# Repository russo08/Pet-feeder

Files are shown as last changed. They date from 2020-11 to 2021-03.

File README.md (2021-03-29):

# Pet-Feeder
Arduino based pet feeder

## Libraries
Here are all the libraries you will need to download  
https://github.com/JChristensen/JC_Button - Buttons library  
https://github.com/VaSe7u/LiquidMenu - Creating the menu  
https://github.com/adafruit/RTClib - Getting time from the RTC  

## 3D Printed Models

All printed using an Ender 3 pro and with the following settings
- Material: PLA+
- Nozzle Temp: 210 C
- Bed Temp: 60 C
- Print speed: 60 mm/s
- Slicer Settings: Use Standard default Cura settings (except printing temp and print speed)

## Funnel, Servo Bracket, and Food Chute, and Chute Rail Supports
- Support Density: 10% for all
- Support placement for funnel: Touching buildplate
- Support placement for bracket: Everywhere
- Support placement for food chute: Touching buildplate
- Support placement for chute rail: Touching buildplate

## Model Orientation in slicer
- Print chute rail standing up with rear (closed off section) touching the build plate
- Print bracket with front touching build plate for minimal support

**NOTE:** The food chute takes up the maximum amount of print surface from the Ender 3. If you plan on using 
a printer with a smaller bed size, the food chute will not fit. In order to get the chute to fit on the slicer, the bottom of the chute 
should be touching the build plate and oriented diagonally on the build surface. It takes a little messing around with, but it will
eventually snap into place.

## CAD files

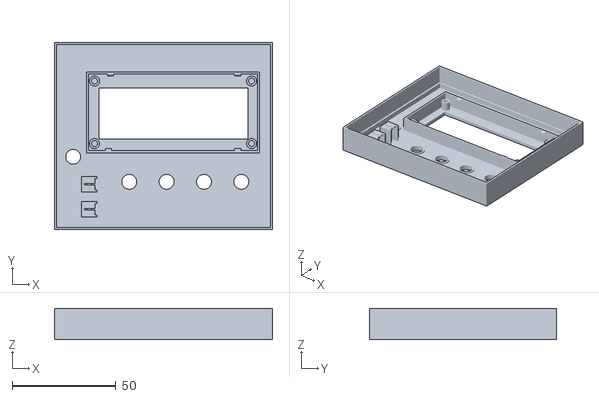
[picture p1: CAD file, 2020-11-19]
STLs/Enclosure_lid2.stl
105.0 x 90.0 x 15.0

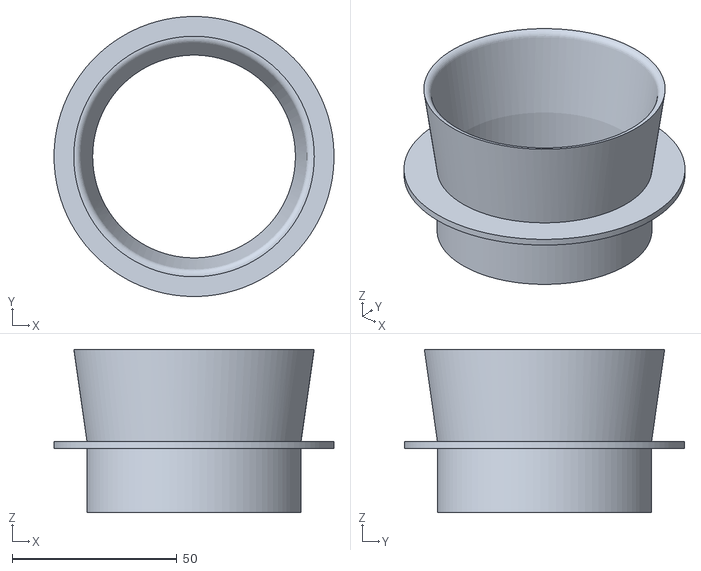
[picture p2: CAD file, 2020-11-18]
STLs/Food_funnel.stl
85.0 x 85.0 x 49.5

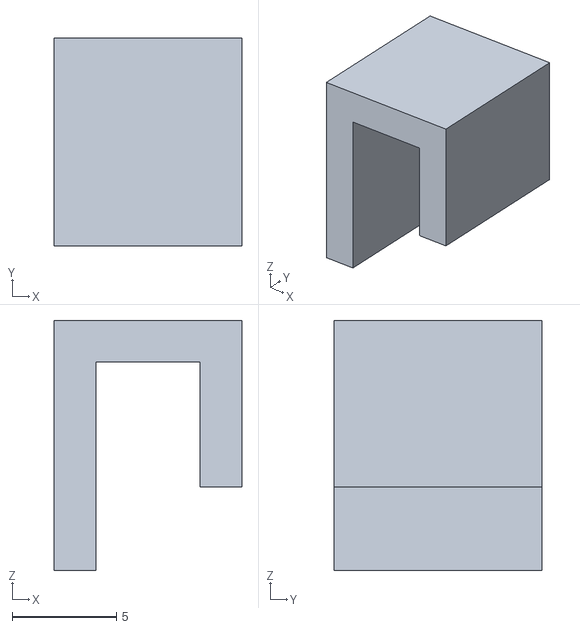
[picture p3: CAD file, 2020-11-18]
STLs/Wire_clip.stl
9.00 x 10.0 x 12.0

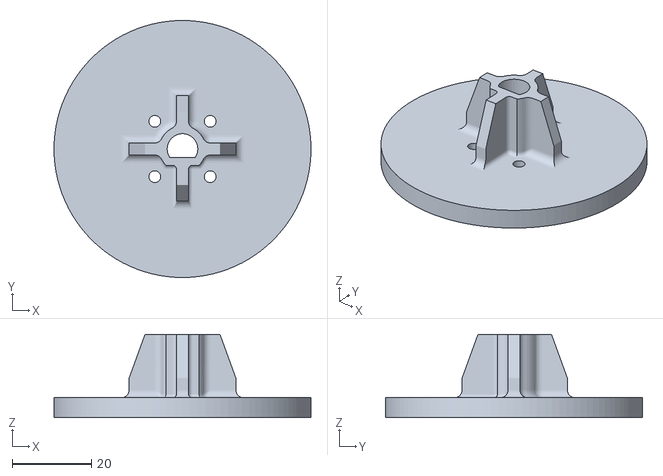
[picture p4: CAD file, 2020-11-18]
STLs/Encoder_Wheel.stl
65.0 x 65.0 x 21.0

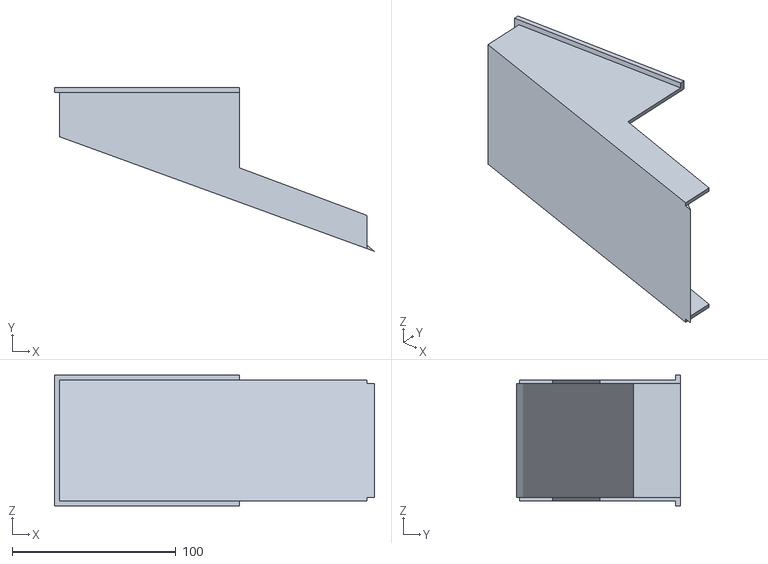
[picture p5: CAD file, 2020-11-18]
STLs/Food_Chute.stl
195.6 x 100.1 x 80.0

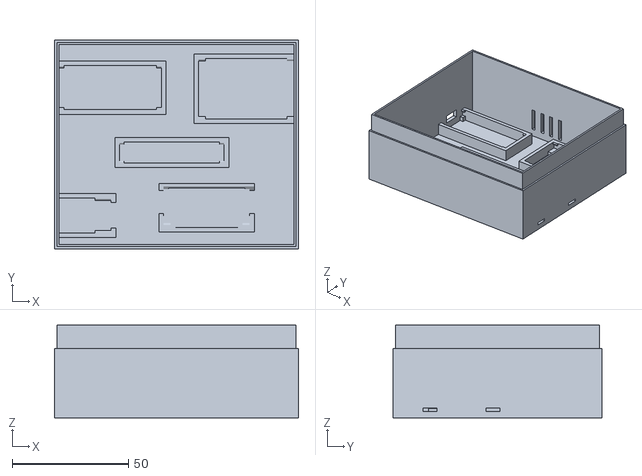
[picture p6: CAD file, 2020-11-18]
STLs/Fedder_Enclosure_bottom.stl
105.0 x 90.0 x 40.0

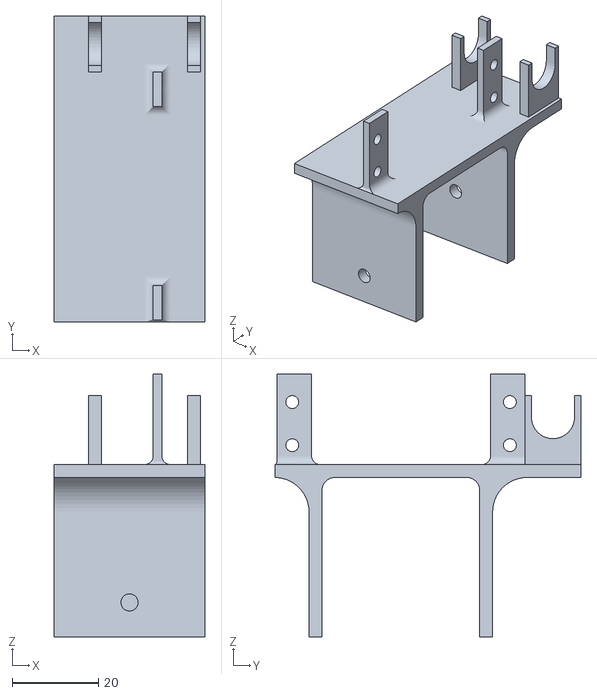
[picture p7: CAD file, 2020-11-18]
STLs/Servo_bracket.stl
35.0 x 71.0 x 61.0

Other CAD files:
Fusion_360_files/Enclosure_lid2 .f3d
Fusion_360_files/Encoder_Wheel.f3d
Fusion_360_files/Fedder_Enclosure_bottom.f3d
Fusion_360_files/Food_Chute v4.f3d
Fusion_360_files/Food_funnel.f3d
Fusion_360_files/Servo_bracket v13.f3d
Fusion_360_files/Wire_clip v2.f3d
Fusion_360_files/Wire_clip.f3d

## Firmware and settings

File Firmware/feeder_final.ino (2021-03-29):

// Final version for the pet feeder

/*  Features:
    - Easy to navigate menu
    - Overview of feed times, current time, feeding comletions,
      and feeding portion on the main screen
    - Controllable portions using a hall sensor for feedback
    - Accurate time keeping with DS1307 chip
    - Can manually change set time in DS1307 chip
    - Two feedings per day
    - Manual feeding option
    - Feeding restart in case of power outtage
    - LED indication of hall sensor and real time clock
    - Feeding times and completions safetly store in EEPROM
    - Servo "jiggle" in the event of food getting stuck
*/

#include <JC_Button.h>
#include <Wire.h>
#include <LiquidCrystal_I2C.h>
#include <LiquidMenu.h>
#include <RTClib.h>
#include <Servo.h>
#include <EEPROM.h>

// Creates servo object to control your servo
Servo myservo;

// Assigning all my I/O pins
#define ENTER_BUTTON_PIN 11
#define UP_BUTTON_PIN 10
#define DOWN_BUTTON_PIN 9
#define BACK_BUTTON_PIN 8
#define POWER_LED_PIN 5
#define MANUAL_BUTTON_PIN A1
#define hallPin 2
#define HALL_LED_PIN 7
#define SERVO_PIN 6

// Defining all the Buttons using the JC_Button library
Button enterBtn (ENTER_BUTTON_PIN);
Button upBtn (UP_BUTTON_PIN);
Button downBtn (DOWN_BUTTON_PIN);
Button backBtn (BACK_BUTTON_PIN);
Button manualFeedBtn (MANUAL_BUTTON_PIN);

// Defining LCD I2C and RTC
LiquidCrystal_I2C lcd(0x27, 16, 2);
RTC_DS1307 rtc;

//Variables used throughout the code

unsigned long hallSensorTime;
unsigned long rotationTime = 400;
unsigned long led_previousMillis = 0;
const long interval_delay = 1000;
unsigned long delay_interval = 2000;
int ledState = LOW;

boolean manualFeed = false;
boolean hall_sensor_fail = false;

unsigned long blink_previousMillis = 0;
unsigned long blink_currentMillis = 0;
unsigned long blink_interval = 500;

unsigned long delay_currentMillis = 0;
unsigned long delay_previousMillis = 0;

boolean blink_state = false;
int count;
boolean feeding1_complete = false;
boolean feeding2_complete = false;
boolean feeding1_trigger = false;
boolean feeding2_trigger = false;
boolean servoOn = true;

//Hall sensor interrupt

volatile boolean hallSensorActivated = false;
volatile int isr_count = 1;
void hallActiveISR()
{
  hallSensorActivated = true;
  digitalWrite(HALL_LED_PIN, HIGH);
  isr_count = isr_count + 1;
}

/* I use enums here to keep better track of what button is
    being pushed as opposed to just having each button set to
    an interger value from 0-3.
*/
enum {
  btnENTER,
  btnUP,
  btnDOWN,
  btnBACK,
};

/* States of the State Machine. Same thing here with the enum
   type. It makes it easier to keep track of what menu you are
   in or want to go to instead of giving each menu an intreger value
*/
enum STATES {
  MAIN,
  MENU_EDIT_FEED1,
  MENU_EDIT_FEED2,
  MENU_EDIT_TIME,
  MENU_EDIT_PORTION,

  EDIT_FEED1_HOUR,
  EDIT_FEED1_MIN,

  EDIT_FEED2_HOUR,
  EDIT_FEED2_MIN,

  EDIT_HOUR,
  EDIT_MIN,

  EDIT_PORTION
};

// Holds state of the state machine
STATES state;

//User input variables
int Hour;
int Minute;
int portion;

int feed_time1_hour;
int feed_time1_min;
int feed_time2_hour;
int feed_time2_min;

int userInput;

// Special character check mark
byte check_Char[8] = {
  B00000,
  B00000,
  B00001,
  B00011,
  B10110,
  B11100,
  B11000,
  B00000
};
//======================The Setup===========================

void setup() {
  Wire.begin();
  Serial.begin(9600);
  lcd.init();
  lcd.backlight();
  lcd.createChar(0, check_Char);

  if (!rtc.begin()) {
    Serial.println("Couldn't find RTC!");
  }

  //  rtc.adjust(DateTime(F(__DATE__), F(__TIME__)));

  //The buttons
  enterBtn.begin();
  upBtn.begin();
  downBtn.begin();
  backBtn.begin();
  manualFeedBtn.begin();

  //Setting up initial state of State Machine
  state = MAIN;

  //Setting up inputs and outputs
  pinMode(POWER_LED_PIN, OUTPUT);
  pinMode(HALL_LED_PIN, OUTPUT);
  pinMode(hallPin, INPUT);

  /* Attatching interrupt to the pin that connects to the hall sensor.
     The hall sensor I used is set to HIGH and goes LOW when it encounters
     a magnet. Thats why its set to FALLING
  */
  attachInterrupt (digitalPinToInterrupt(hallPin), hallActiveISR, FALLING);
  // default state of LEDs
  digitalWrite(POWER_LED_PIN, HIGH);
  digitalWrite (HALL_LED_PIN, LOW);

  /* These functions get the stored feed time, completed feeding,
     and portion size from EEPROM on start-up. I did this because I get random
     power outtages here where I live.
  */
  get_feed_time1();
  get_feed_time2();
  get_completed_feedings();
  get_portion();

}

//======================The Loop===========================
void loop() {
  changing_states();

  check_buttons();

  check_feedtime ();

  check_rtc();

  manual_feed_check ();

  check_hall_sensor();
  Serial.println("Count");
  Serial.println(count);
  Serial.println("ISR Count");
  Serial.println(isr_count);
  Serial.println("Hall");
  Serial.println(hall_sensor_fail);
}

//=============== The Functions =======================

/* Uses the JC_Button Library to continually check if a button
   was pressed. Depending on what button is pressed, it sets the
   variable userInput to be used in the fucntion menu_transitions
*/
void check_buttons () {
  enterBtn.read();
  upBtn.read();
  downBtn.read();
  backBtn.read();
  manualFeedBtn.read();

  if (enterBtn.wasPressed()) {
    Serial.println ("You Pressed Enter!");
    userInput = btnENTER;
    menu_transitions(userInput);
  }
  if (upBtn.wasPressed()) {
    Serial.println ("You Pressed Up!");
    userInput = btnUP;
    menu_transitions(userInput);
  }
  if (downBtn.wasPressed()) {
    Serial.println ("You Pressed Down!");
    userInput = btnDOWN;
    menu_transitions(userInput);
  }
  if (backBtn.wasPressed()) {
    Serial.println ("You Pressed Back!");
    userInput = btnBACK;
    menu_transitions(userInput);
  }
  if (manualFeedBtn.wasPressed()) {
    Serial.println ("You Are Manually Feeding!");
    manualFeed = true;
  }
}
//=====================================================

/* This funcion determines what is displayed, depending on what menu
    or "state" you are in. Each menu has a function that displays the
    respective menu
*/
void changing_states() {

  switch (state) {
    case MAIN:
      display_current_time();
      display_feeding_times();
      display_portion();
      break;

    case MENU_EDIT_FEED1:
      display_set_feed_time1_menu();
      break;

    case MENU_EDIT_FEED2:
      display_set_feed_time2_menu();
      break;

    case MENU_EDIT_TIME:
      display_set_time_menu();
      break;

    case MENU_EDIT_PORTION:
      display_set_portion_menu ();
      break;

    case EDIT_FEED1_HOUR:
      set_feed_time1();
      break;

    case EDIT_FEED1_MIN:
      set_feed_time1();
      break;

    case EDIT_FEED2_HOUR:
      set_feed_time2();
      break;

    case EDIT_FEED2_MIN:
      set_feed_time2();
      break;

    case EDIT_HOUR:
      set_the_time();
      break;

    case EDIT_MIN:
      set_the_time();
      break;

    case EDIT_PORTION:
      set_the_portion();
      break;
  }
}
//=====================================================
/* This is the transitional part of the state machine. This is
   what allows you to go from one menu to another and change values
*/
void menu_transitions(int input) {

  switch (state) {
    case MAIN:
      if (input == btnENTER) {
        lcd.clear();
        state = MENU_EDIT_FEED1;
      }
      if (input == btnBACK)
      {
        hall_sensor_fail = false;
      }
      break;
    //----------------------------------------------------
    case MENU_EDIT_FEED1:
      if (input == btnBACK) {
        lcd.clear();
        state = MAIN;
      }
      else if (input == btnENTER) {
        lcd.clear();
        state = EDIT_FEED1_HOUR;
      }
      else if (input == btnDOWN) {
        lcd.clear();
        state = MENU_EDIT_FEED2;
      }
      break;
    //----------------------------------------------------
    case EDIT_FEED1_HOUR:
      // Need this to prevent servo going off while setting time
      servoOn = false;
      if (input == btnUP) {
        feed_time1_hour++;
        if (feed_time1_hour > 23) {
          feed_time1_hour = 0;
        }
      }
      else if (input == btnDOWN) {
        feed_time1_hour--;
        if (feed_time1_hour < 0) {
          feed_time1_hour = 23;
        }
      }
      else if (input == btnBACK) {
        lcd.clear();
        servoOn = true;
        state = MENU_EDIT_FEED1;
      }
      else if (input == btnENTER) {
        state = EDIT_FEED1_MIN;
      }
      break;
    //----------------------------------------------------
    case EDIT_FEED1_MIN:
      if (input == btnUP) {
        feed_time1_min++;
        if (feed_time1_min > 59) {
          feed_time1_min = 0;
        }
      }
      else if (input == btnDOWN) {
        feed_time1_min--;
        if (feed_time1_min < 0) {
          feed_time1_min = 59;
        }
      }
      else if (input == btnBACK) {
        state = EDIT_FEED1_HOUR;
      }
      else if (input == btnENTER) {
        lcd.clear();
        lcd.setCursor(0, 0);
        lcd.print( "*Settings Saved*");
        delay(1000);
        lcd.clear();
        servoOn = true;
        write_feeding_time1 ();
        state = MAIN;
      }
      break;
    //----------------------------------------------------
    case MENU_EDIT_FEED2:
      if (input == btnUP) {
        lcd.clear();
        state = MENU_EDIT_FEED1;
      }
      else if (input == btnENTER) {
        lcd.clear();
        state = EDIT_FEED2_HOUR;
      }
      else if (input == btnDOWN) {
        lcd.clear();
        state = MENU_EDIT_TIME;
      }
      break;
    //----------------------------------------------------
    case EDIT_FEED2_HOUR:
      servoOn = false;
      if (input == btnUP) {
        feed_time2_hour++;
        if (feed_time2_hour > 23) {
          feed_time2_hour = 0;
        }
      }
      else if (input == btnDOWN) {
        feed_time2_hour--;
        if (feed_time2_hour < 0) {
          feed_time2_hour = 23;
        }
      }
      else if (input == btnBACK) {
        lcd.clear();
        servoOn = true;  
        state = MENU_EDIT_FEED2;
      }
      else if (input == btnENTER) {
        state = EDIT_FEED2_MIN;
      }
      break;
    //----------------------------------------------------
    case EDIT_FEED2_MIN:
      if (input == btnUP) {
        feed_time2_min++;
        if (feed_time2_min > 59) {
          feed_time2_min = 0;
        }
      }
      else if (input == btnDOWN) {
        feed_time2_min--;
        if (feed_time2_min < 0) {
          feed_time2_min = 59;
        }
      }
      else if (input == btnBACK) {
        state = EDIT_FEED2_HOUR;
      }
      else if (input == btnENTER) {
        lcd.clear();
        lcd.setCursor(0, 0);
        lcd.print( "*Settings Saved*");
        delay(1000);
        lcd.clear();
        servoOn = true;
        write_feeding_time2 ();
        state = MAIN;
      }
      break;
    //----------------------------------------------------
    case MENU_EDIT_TIME:
      if (input == btnUP) {
        lcd.clear();
        state = MENU_EDIT_FEED2;
      }
      else if (input == btnENTER) {
        lcd.clear();
        state = EDIT_HOUR;
      }
      else if (input == btnDOWN) {
        lcd.clear();
        state = MENU_EDIT_PORTION;
      }
      break;
    //----------------------------------------------------
    case EDIT_HOUR:
      if (input == btnUP) {
        Hour++;
        if (Hour > 23) {
          Hour = 0;
        }
      }
      else if (input == btnDOWN) {
        Hour--;
        if (Hour < 0) {
          Hour = 23;
        }
      }
      else if (input == btnBACK) {
        lcd.clear();
        state = MENU_EDIT_TIME;
      }
      else if (input == btnENTER) {
        state = EDIT_MIN;
      }
      break;
    //----------------------------------------------------
    case EDIT_MIN:
      if (input == btnUP) {
        Minute++;
        if (Minute > 59) {
          Minute = 0;
        }
      }
      else if (input == btnDOWN) {
        Minute--;
        if (Minute < 0) {
          Minute = 59;
        }
      }
      else if (input == btnBACK) {
        state = EDIT_HOUR;
      }
      else if (input == btnENTER) {
        lcd.clear();
        lcd.setCursor(0, 0);
        lcd.print( "*Settings Saved*");
        delay(1000);
        lcd.clear();
        rtc.adjust(DateTime(0, 0, 0, Hour, Minute, 0));
        state = MAIN;
      }
      break;
    //----------------------------------------------------
    case MENU_EDIT_PORTION:
      if (input == btnUP) {
        lcd.clear();
        state = MENU_EDIT_TIME;
      }
      else if (input == btnENTER) {
        lcd.clear();
        state = EDIT_PORTION;
      }
      break;
    //----------------------------------------------------
    case EDIT_PORTION:
      if (input == btnUP) {
        portion++;
        if (portion > 20) {
          portion = 1;
        }
      }
      else if (input == btnDOWN) {
        portion--;
        if (portion < 1) {
          portion = 20;
        }
      }
      else if (input == btnBACK) {
        lcd.clear();
        state = MENU_EDIT_PORTION;
      }
      else if (input == btnENTER) {
        lcd.clear();
        lcd.setCursor(0, 0);
        lcd.print( "*Settings Saved*");
        delay(1000);
        lcd.clear();
        write_portion();
        state = MAIN;
      }
      break;
  }
}
//=====================================================
// This function checks the feed time against the current time

void check_feedtime ()
{
  DateTime now = rtc.now();
  if (now.second() == 0) {
    if ((now.hour() == feed_time1_hour) && (now.minute() == feed_time1_min))
    {
      feeding1_trigger = true;
      if (servoOn)
      {
        if (feeding1_complete == false)
        {
          lcd.clear();
          lcd.setCursor(3, 0);
          lcd.print ("Dispensing");
          lcd.setCursor(1, 1);
          lcd.print("First Feeding");
          startFeeding();
        }
      }
    }
    else if ((now.hour() == feed_time2_hour) && (now.minute () == feed_time2_min))
    {
      feeding2_trigger = true;
      if (servoOn)
      {
        if ( feeding2_complete == false)
        {
          lcd.clear();
          lcd.setCursor(3, 0);
          lcd.print ("Dispensing");
          lcd.setCursor(0, 1);
          lcd.print("Second Feeding");
          startFeeding();
        }
      }
    }
  }
  // Midnight Reset
  if ( (now.hour() == 0) && (now.minute() == 0))
  {
    feeding1_complete = false;
    feeding2_complete = false;
    EEPROM.write(4, feeding1_complete);
    EEPROM.write(5, feeding2_complete);
  }
  /*If power outtage happens during a feed time, this checks to see if the
     feed time has passed and if the feeding occurred. If not, it feeds.
  */
  if ( (now.hour() >= feed_time1_hour) && (now.minute() > feed_time1_min))
  {
    if ((feeding1_complete == 0) && (feeding1_trigger == 0))
    {
      lcd.clear();
      lcd.setCursor(5, 0);
      lcd.print ("Uh-Oh!");
      lcd.setCursor(2, 1);
      lcd.print("Power Outage");
      startFeeding();
    }
  }
  if ( (now.hour() >= feed_time2_hour) && (now.minute() > feed_time2_min))
  {
    if ((feeding2_complete == 0) && (feeding2_trigger == 0))
    {
      lcd.clear();
      lcd.setCursor(5, 0);
      lcd.print ("Uh-Oh!");
      lcd.setCursor(2, 1);
      lcd.print("Power Outage");
      startFeeding();
    }
  }
}

//=====================================================
// Displays the set portion menu option
void display_set_portion_menu () {
  lcd.setCursor(2, 0);
  lcd.print("Menu Options");
  lcd.setCursor(0, 1);
  lcd.print("Set the Portion");
}
//=====================================================
// Displays the menu where you change the current time
void set_the_time ()
{
  lcd.setCursor(2, 0);
  lcd.print("Set the Time");
  switch (state)
  {
    //----------------------------------------------------
    case EDIT_HOUR:

      if (blink_state == 0)
      {
        lcd.setCursor(5, 1);
        add_leading_zero(Hour);
      }
      else
      {
        lcd.setCursor(5, 1);
        lcd.print("  ");
      }
      lcd.print(":");
      add_leading_zero(Minute);
      break;
    //----------------------------------------------------
    case EDIT_MIN:
      lcd.setCursor(5, 1);
      add_leading_zero(Hour);
      lcd.print(":");
      if (blink_state == 0)
      {
        lcd.setCursor(8, 1);
        add_leading_zero(Minute);
      }
      else
      {
        lcd.setCursor(8, 1);
        lcd.print("  ");
      }
      break;
  }
  blinkFunction();
}
//=====================================================
// Displays the menu where you change the feeding portion
void set_the_portion ()
{
  lcd.setCursor (0, 0);
  lcd.print("Set the Portion");
  switch (state)
  {
    case EDIT_PORTION:
      if (blink_state == 0)
      {
        lcd.setCursor(7, 1);
        add_leading_zero(portion);
      }
      else
      {
        lcd.setCursor(7, 1);
        lcd.print("  ");
      }
  }
  blinkFunction();
}
//=====================================================
//Displays the menu option for setting the time
void display_set_time_menu () {
  lcd.setCursor(2, 0);
  lcd.print("Menu Options");
  lcd.setCursor(2, 1);
  lcd.print("Set the Time");
}
//=====================================================
// Displays the menu where you change the second feeding time
void set_feed_time2 ()
{
  lcd.setCursor(0, 0);
  lcd.print("Set Feed Time 2");
  switch (state)
  {
    //----------------------------------------------------
    case EDIT_FEED2_HOUR:

      if (blink_state == 0)
      {
        lcd.setCursor(5, 1);
        add_leading_zero(feed_time2_hour);
      }
      else
      {
        lcd.setCursor(5, 1);
        lcd.print("  ");
      }
      lcd.print(":");
      add_leading_zero(feed_time2_min);
      break;
    //----------------------------------------------------
    case EDIT_FEED2_MIN:
      lcd.setCursor(5, 1);
      add_leading_zero(feed_time2_hour);
      lcd.print(":");
      if (blink_state == 0)
      {
        lcd.setCursor(8, 1);
        add_leading_zero(feed_time2_min);
      }
      else
      {
        lcd.setCursor(8, 1);
        lcd.print("  ");
      }
      break;
  }
  blinkFunction();
}
//=====================================================
// Displays the menu where you change the first feeding time
void set_feed_time1 ()
{
  lcd.setCursor(0, 0);
  lcd.print("Set Feed Time 1");
  switch (state)
  {
    //----------------------------------------------------
    case EDIT_FEED1_HOUR:

      if (blink_state == 0)
      {
        lcd.setCursor(5, 1);
        add_leading_zero(feed_time1_hour);
      }
      else
      {
        lcd.setCursor(5, 1);
        lcd.print("  ");
      }
      lcd.print(":");
      add_leading_zero(feed_time1_min);
      break;
    //----------------------------------------------------
    case EDIT_FEED1_MIN:
      lcd.setCursor(5, 1);
      add_leading_zero(feed_time1_hour);
      lcd.print(":");
      if (blink_state == 0)
      {
        lcd.setCursor(8, 1);
        add_leading_zero(feed_time1_min);
      }
      else
      {
        lcd.setCursor(8, 1);
        lcd.print("  ");
      }
      break;
  }
  blinkFunction();
}
//=====================================================
// Adds a leading zero to single digit numbers
void add_leading_zero (int num) {
  if (num < 10) {
    lcd.print("0");
  }
  lcd.print(num);
}
//=====================================================
/* Displays the feeding time on the main menu as well as the
   check mark for visual comfirmation of a completed feeding
*/
void display_feeding_times () {
  //Displaying first feed time
  lcd.setCursor(0, 0);
  lcd.print ("F1:");
  add_leading_zero(feed_time1_hour);
  lcd.print(":");
  add_leading_zero(feed_time1_min);
  lcd.print(" ");
  if (feeding1_complete == true)
  {
    lcd.write(0);
  }
  else
  {
    lcd.print(" ");
  }
  //Displaying second feed time
  lcd.setCursor(0, 1);
  lcd.print("F2:");
  add_leading_zero(feed_time2_hour);
  lcd.print(":");
  add_leading_zero(feed_time2_min);
  lcd.print(" ");
  if (feeding2_complete == true)
  {
    lcd.write(0);
  }
  else
  {
    lcd.print(" ");
  }
}
//=====================================================
// Displays the current time in the main menu
void display_current_time () {
  DateTime now = rtc.now();
  lcd.setCursor(11, 0);
  add_leading_zero(now.hour());
  lcd.print(":");
  add_leading_zero(now.minute());
}
//=====================================================
// Displays the menu option for setting the first feed time
void display_set_feed_time1_menu () {
  lcd.setCursor(2, 0);
  lcd.print("Menu Options");
  lcd.setCursor(0, 1);
  lcd.print("Set Feed Time 1");
}
//=====================================================
// Displays the meny option for setting the second feed time
void display_set_feed_time2_menu () {
  lcd.setCursor(2, 0);
  lcd.print("Menu Options");
  lcd.setCursor(0, 1);
  lcd.print("Set Feed Time 2");
}
//=====================================================
// Displays the feeding portion in the main menu
void display_portion ()
{
  lcd.setCursor (12, 1);
  lcd.print("P:");
  add_leading_zero(portion);
}
//=====================================================
// Starts the feeding process.
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

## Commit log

2020-11-24 Fix a bug with sevoOn
    When navigating through menus, if you go into the EDIT_FEED#_HOUR menus and then go back, servoOn will never be reset to true. Feeding will never happen.
    [feeder_final.ino]
2020-11-30 Rename Arduino Code/feeder_final.ino to Firmware/feeder_final.ino
